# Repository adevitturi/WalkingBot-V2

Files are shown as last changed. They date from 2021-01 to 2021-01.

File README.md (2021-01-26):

# WalkingBot-V2
WalkingBot-V2 is an open source 3D printed robot that walks!
This repository contains all the software, 3D models and BOM to make the full assembly.

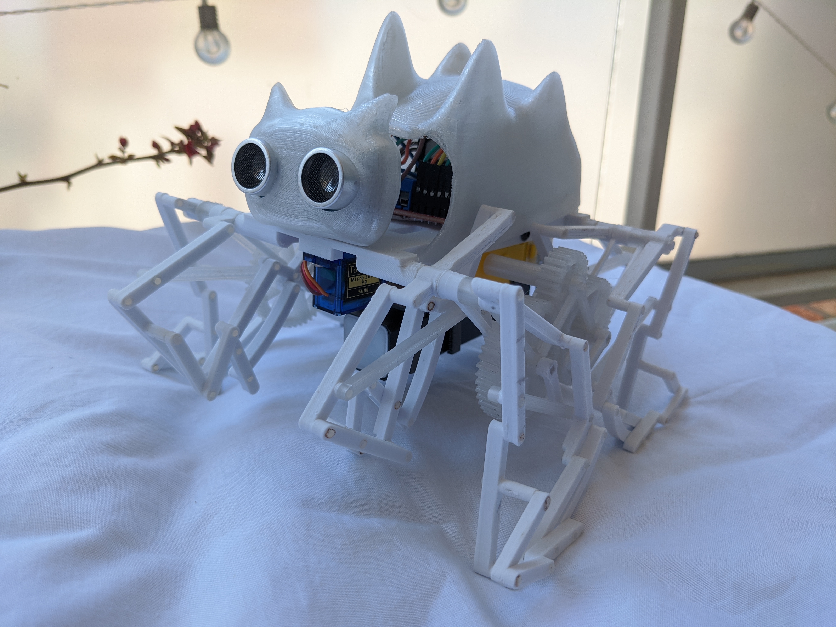
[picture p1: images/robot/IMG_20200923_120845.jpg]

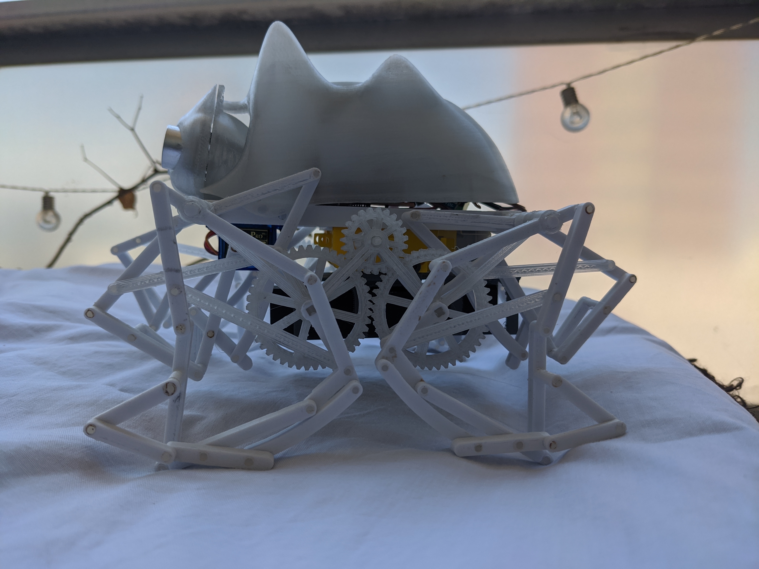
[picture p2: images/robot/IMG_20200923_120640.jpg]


## About
I think my strongest motivation for building walking mechanisms arised after discovering the marvelous [strandbeests by Theo Jansen][1].
After doing some further research on the topic, I found some other mechanimsms with different walking profiles. The one that caught my attention the most was the [trotbot][2], so I based my design on it, adding just some small modifications to the linkage structure.

## Hardware
The following table lists the BOM:

|Parts | Quantity | 
|---|---|
| [NodeMCU board][3] | 1 |
| [L298 N H-Bridge driver][4]  | 1 |
| [18650 battery holder][5] | 1 |
| [18650 batteries][6] | 2 |
| [BMS 2S battery charger][7]  | 1 |
| [cables and connectors][11]  | 2 |
| [ultrasound sensor][8] | 1 |
| [dc motors with gearbox][9]  | 2 |
| [SG90 Servo 180 degrees][10] | 1 	 |
| M3x25 bolts | 4 	 |
| M3x12 bolts | 2 	 |
| M3 nuts | 4 	 |
 
 To see the circuit diagram [click here!](docs/circuit_diagram.md)
 
 ## 3D printed parts and assembly
 STL files can be found under [parts/STL](parts/STL).
 
 The parts were designed using Autodesk Inventor. CAD files and full assemblies can be found under [parts/CAD](parts/CAD).
 
 To see the assembly instructions [click here!](docs/assembly.md)
 
 ## Software
 The robot can be controlled throw Wi-Fi using MQTT messages. For this project we see how to control it with a joystick on an Android App called [Remote XY][12].
 
 The software in this repository includes:
  - Firmware: Arduino sketch for the NodeMCU board.
  - Node-RED flow: a server in charge of communicating the joystick in the phone with the robot.

 To see a guide for setting up the software [click here!](docs/software.md)
 
 ## Videos
 https://youtu.be/vDro2LflieM

 https://youtu.be/8G8XOwB4iCY

 https://youtu.be/JpEi38m9lwI
 
 https://youtu.be/GgEGYwh3bX8
  
 ## Authors

- [Agustin Devitturi](https://github.com/adevitturi)

[1]: https://www.strandbeest.com/
[2]: https://www.diywalkers.com/trotbot-linkage-plans.html
[3]: https://www.amazon.com/KeeYees-Internet-Development-Wireless-Compatible/dp/B07PR9T5R5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 "NodeMcu"
[4]: https://www.amazon.com/L298N-H-Bridge-Stepper-Module-Arduino/dp/B07D2BTMPK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 "L298 Driver"
[5]: https://www.amazon.com/HTTX-Battery-Holder-2-Slot-Storage/dp/B07DBLY3WS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 "Battery holder"
[6]: https://www.ebay.com/itm/SAMSUNG-ICR-22P-SDI-2-GN1T-RECHARGEABLE-BATTERIE-3-6V-2150mAh-Li-Ion-NEU/143293064204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 "18650 batteries"
[7]: https://www.amazon.com/-/es/Li-ion-Bater%C3%ADa-Cargador-Protecci%C3%B3n-Sobrecarga/dp/B07GX2VTXC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 "BMS 2S"
[8]: https://www.amazon.com/UIOTEC-Operating-HC-SR04-P-Ultrasound-Ultrasonic/dp/B07DWWTT3F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 "Ultrasound sensor"
[9]: https://www.amazon.com/AutoEC-4pcs-Motor-Smart-Robot/dp/B00U4HP0SQ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
[10]: https://www.amazon.com/SunFounder-Digital-Helicopter-Airplane-Controls/dp/B01M5LIKLQ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 "Servo"
[11]:https://www.amazon.com/-/es/10-pares-Connector-Battery-discharge-alambre/dp/B01JUDP5NY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 "Battery connector"
[12]:https://play.google.com/store/apps/details?id=com.shevauto.remotexy.free&hl=es&gl=US

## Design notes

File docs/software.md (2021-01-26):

## Arduino firmware
First you need to install Arduino IDE. you can see an installation guide [here][1].

Download the arduino sketch from [firmware/walkingbot](../firmware/walkingbot).
To upload an arduino sketch to the NodeMcu board you can follow [this guide][2].

The firmware on the NodeMcu subscribes to an MQTT topic `diff_speed` to get the linear and angular speed commands in a range from 0 to 100 to command the motors that drive the leags on each side of the robot.
It also subscribes to the topic `head_dir` that commands the movement of the head. Note that the current model of the head doesn't have a really wide angle of movement. This will be tackled in future versions no make for a wider vision angle.
The firmware also publishes constantly the readings from the ultrasound sensor to the topic `ultrasound`, which represents the distance in centimeters.

## Node-RED
You will require to install Node-RED in your pc. You can see an installation guide [here][3].

You will also need to install and run a MQTT broker. You can use Eclipse Mosquitto, which is an open-source MQTT message broker. You can see an installation guide [here][4].

Once you have node-RED running, download the Node-RED flow from [nodered/robot-control.json](../nodered/robot-control.json) and import it in your browser.
Then you can make sure that all nodes are set up properly and finally click the 'Deploy' button.

## Android Remote XY
You can download the [Remote XY][5] app to your Android device.
Once you run it, you can go to the '+' option, then 'connect to device by IP or URL'.
In the 'Device IP or URL' field enter your local IP address, on which node-RED is running.
In the 'Port' field you can check the selected port in the node-RED configuration for the nodes using Remote XY, in general it is 6377.
Finally you should see a dashboard with a joystick and a control to move the head and see the distance reading.

You can edit the current dashboard in the [Remote XY Editor][6] and then paste the generated code in any node configuration for Remote XY in your node-RED flow.

[1]: https://www.arduino.cc/en/software
[2]: https://www.instructables.com/Quick-Start-to-Nodemcu-ESP8266-on-Arduino-IDE/
[3]: https://nodered.org/docs/getting-started/local
[4]: https://mosquitto.org/download/
[5]: https://play.google.com/store/apps/details?id=com.shevauto.remotexy.free&hl=es&gl=US
[6]: https://remotexy.com/en/editor/

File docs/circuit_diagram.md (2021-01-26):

## Circuit diagram

You can see the whole diagram in the picture below. Or access the image under [images/circuit/circuit_diagram.png](../images/circuit/circuit_diagram.png).

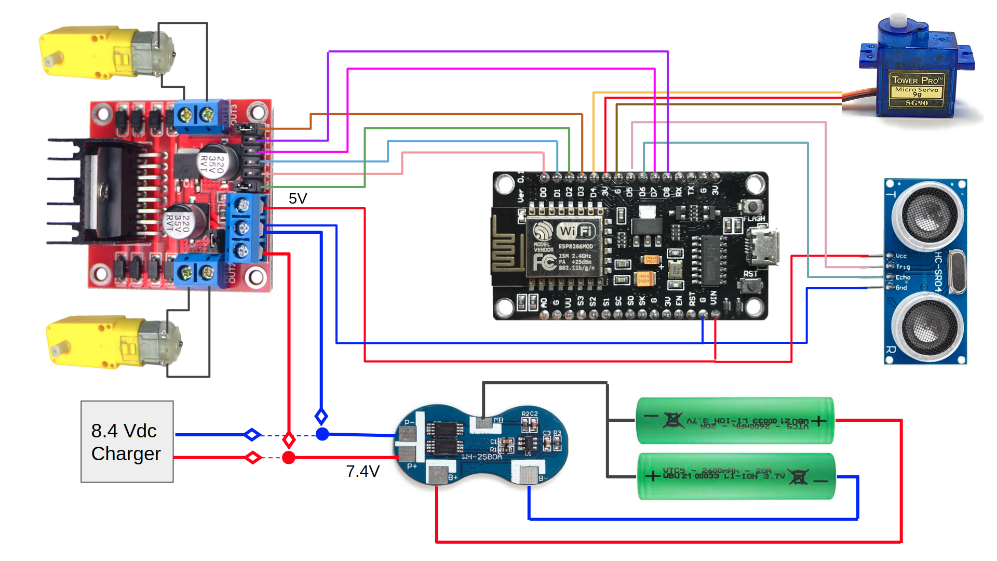
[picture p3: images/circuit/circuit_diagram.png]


To connect all the wires that come out from the NodeMcu you can assemble a small development board with some extra male header pins to make it easier, but you can choose the way that is easier to you.
In the following picture you can see an example board with some extra header pins to connect some dupont cables.

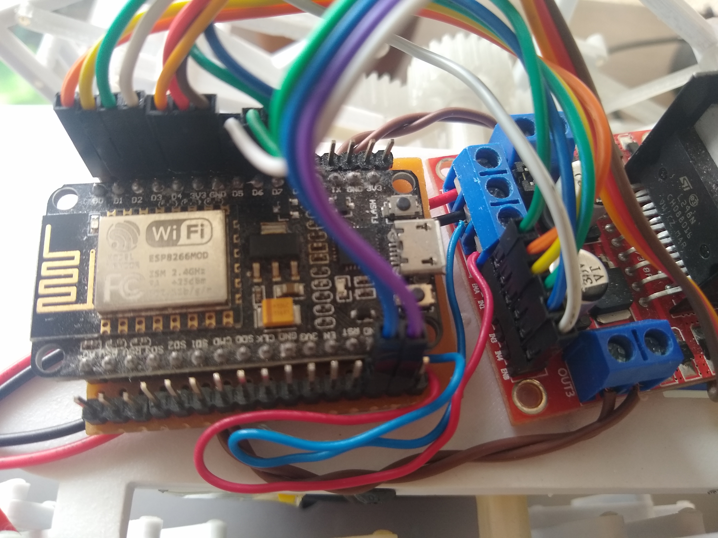
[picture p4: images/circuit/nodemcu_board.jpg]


You will notice that to make the connections in the robot head there is a hole where you can connect some duppont cables.

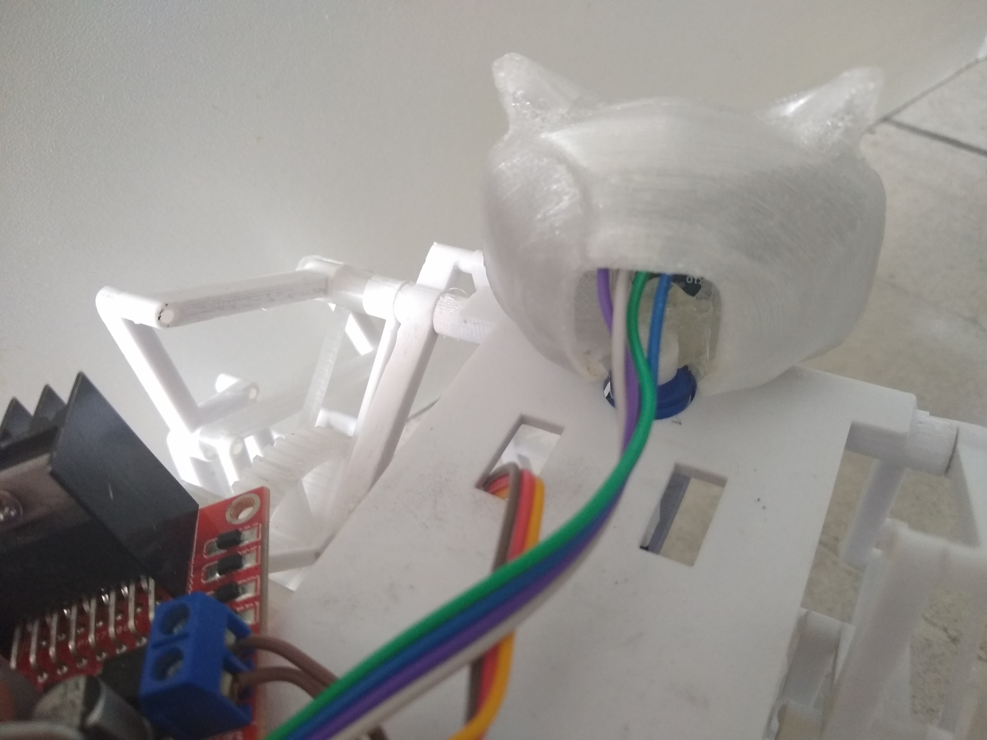
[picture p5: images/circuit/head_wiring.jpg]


To connect the motors, the servo and the batteries, you will notice there are some square holes in the robot chasis from where you can pull the cables from the other side.

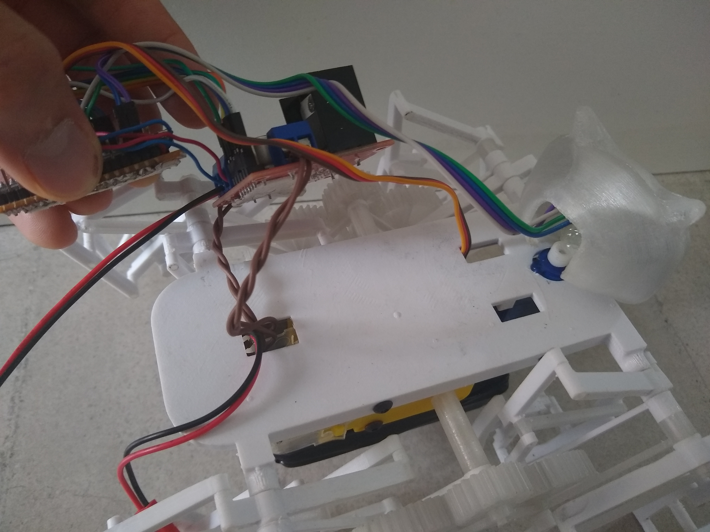
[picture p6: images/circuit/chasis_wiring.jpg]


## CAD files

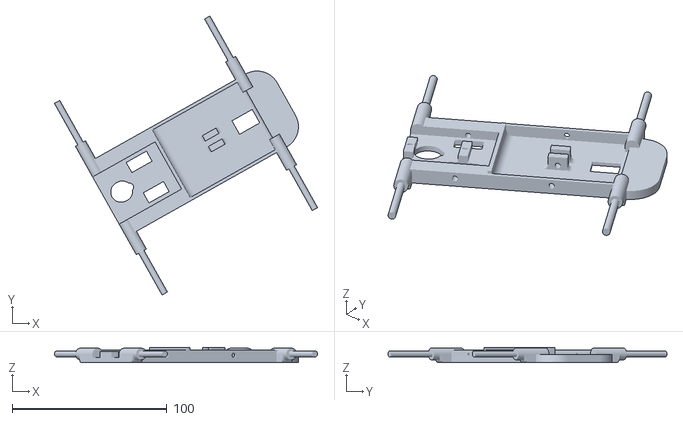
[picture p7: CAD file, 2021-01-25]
parts/STL/body/chasis.stl
170.1 x 180.3 x 9.42

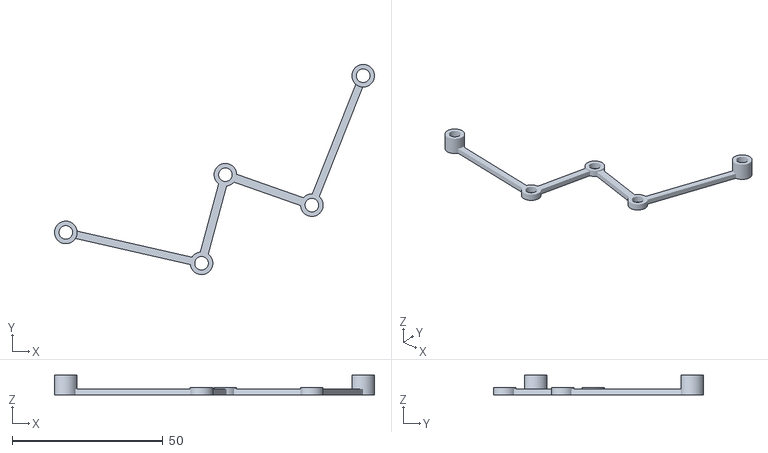
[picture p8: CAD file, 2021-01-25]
parts/STL/gears/gear-holder.stl
106.0 x 69.6 x 6.50

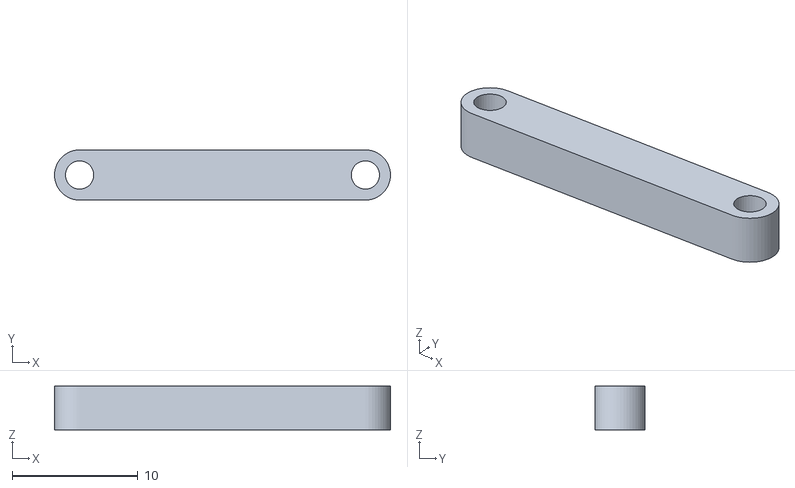
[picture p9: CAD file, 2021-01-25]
parts/STL/leg/toe1.stl
26.8 x 4.00 x 3.50

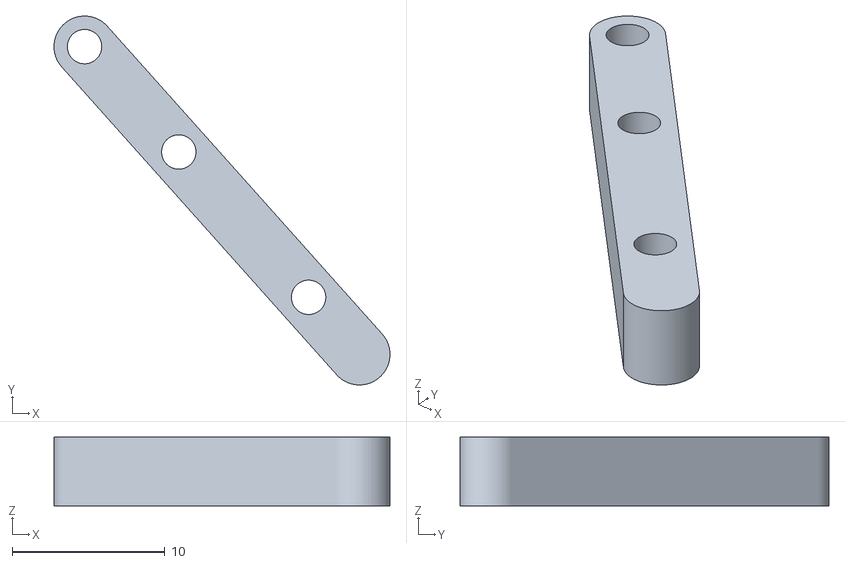
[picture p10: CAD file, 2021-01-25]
parts/STL/leg_mirrored/bone3_MIR.stl
22.0 x 24.1 x 4.50

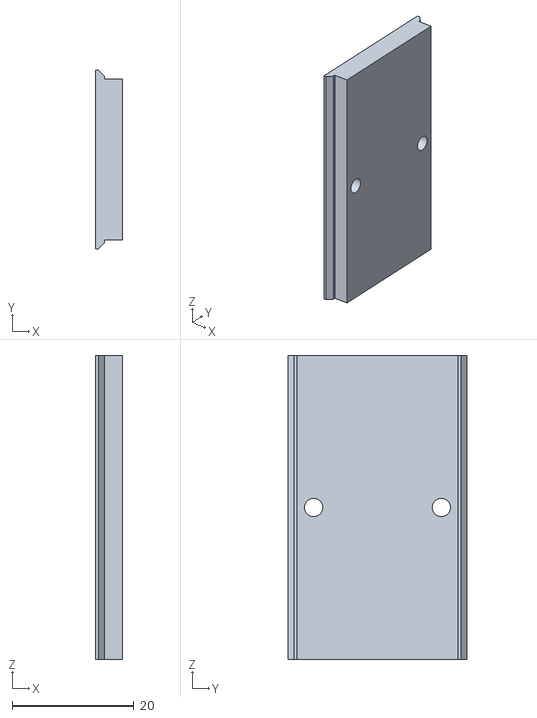
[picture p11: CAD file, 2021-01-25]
parts/STL/body/batter-holder.stl
4.50 x 29.5 x 50.0

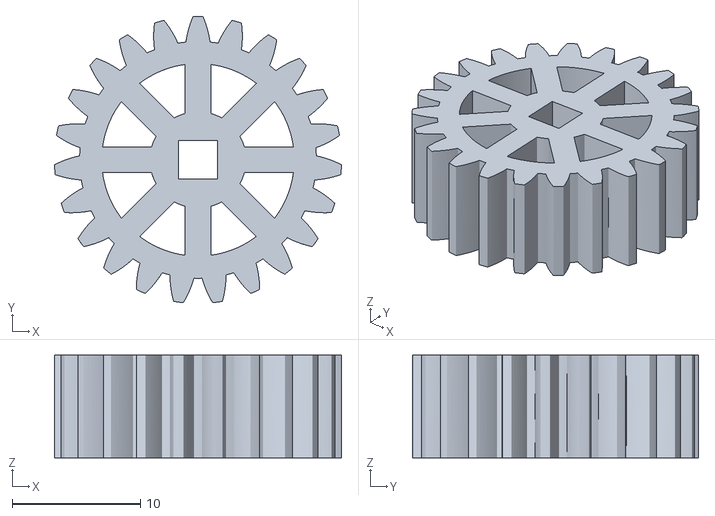
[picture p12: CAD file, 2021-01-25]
parts/STL/gears/small-gear.stl
22.4 x 22.3 x 8.00

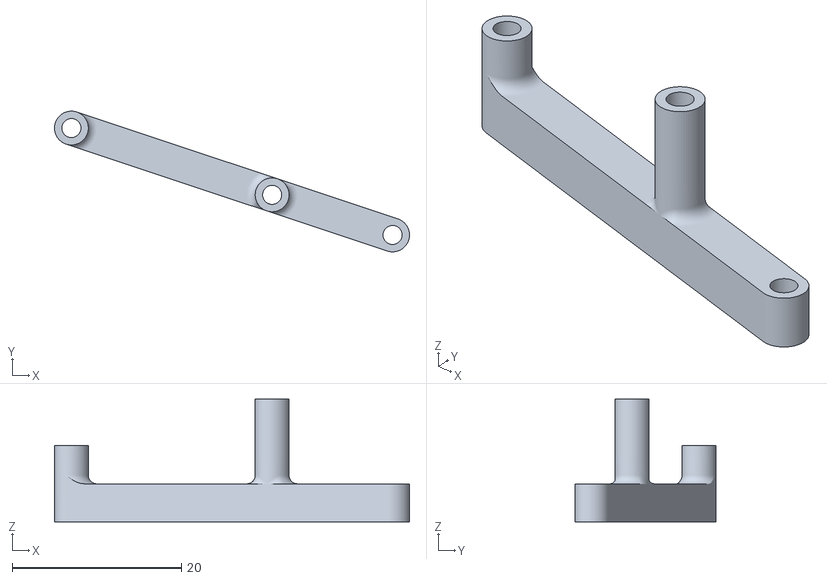
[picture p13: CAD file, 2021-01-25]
parts/STL/leg/bone4.stl
42.0 x 16.6 x 14.5

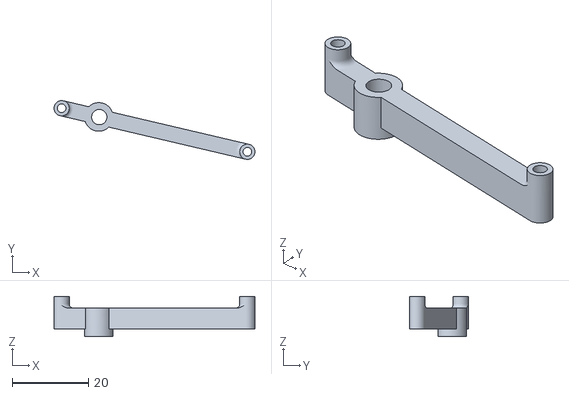
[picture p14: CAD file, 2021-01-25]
parts/STL/leg_mirrored/bone0_MIR.stl
52.7 x 15.4 x 10.5

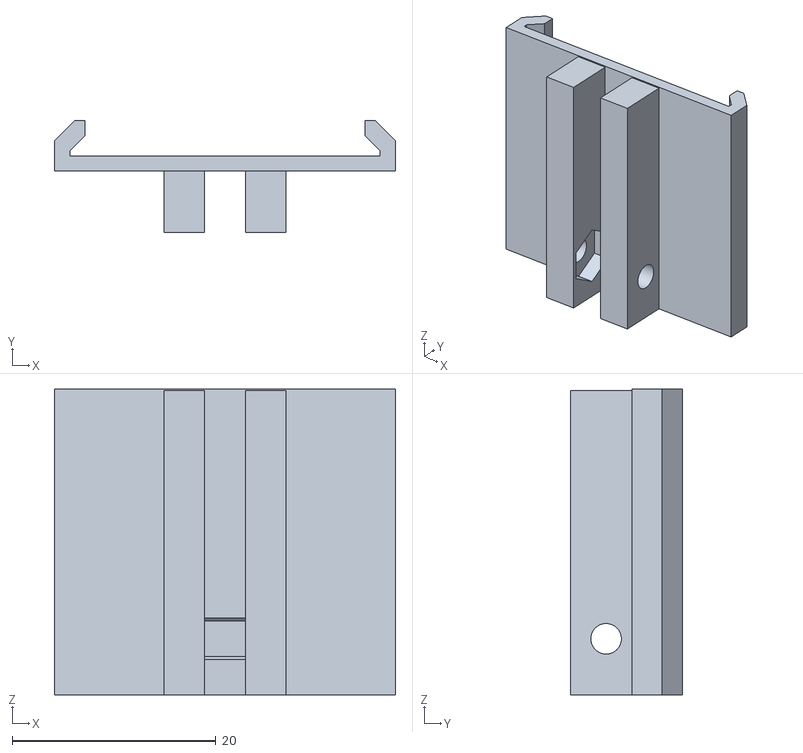
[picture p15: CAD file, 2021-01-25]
parts/STL/body/battery-holder-robot.stl
33.5 x 11.0 x 30.0

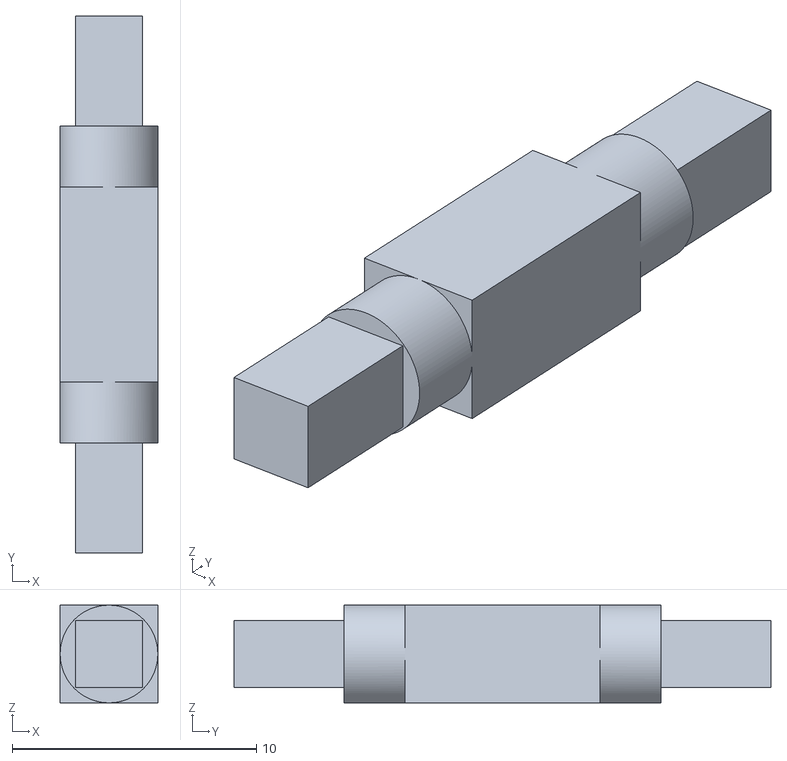
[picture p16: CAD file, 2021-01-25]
parts/STL/gears/gear2-shaft.stl
4.00 x 22.0 x 4.00

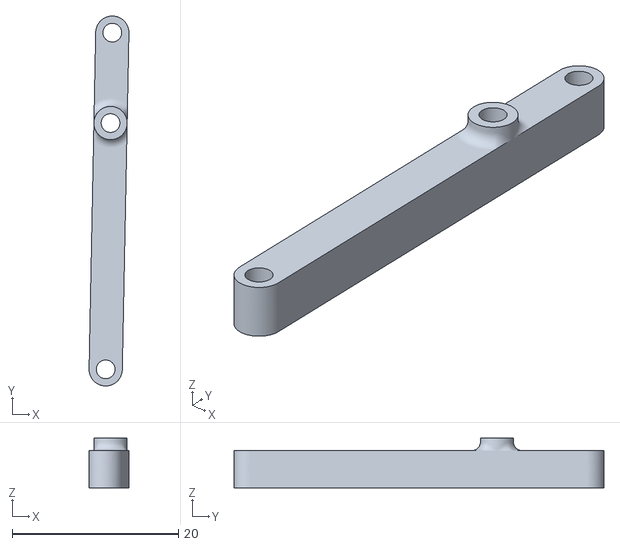
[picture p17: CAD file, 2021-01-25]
parts/STL/leg/bone5.stl
4.80 x 44.5 x 6.00

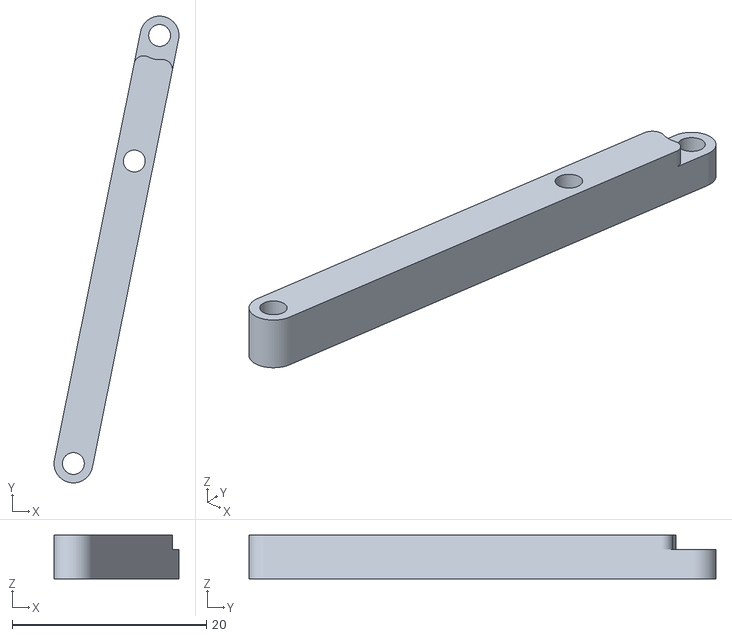
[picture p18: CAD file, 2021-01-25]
parts/STL/leg_mirrored/bone1_MIR.stl
12.9 x 48.1 x 4.50

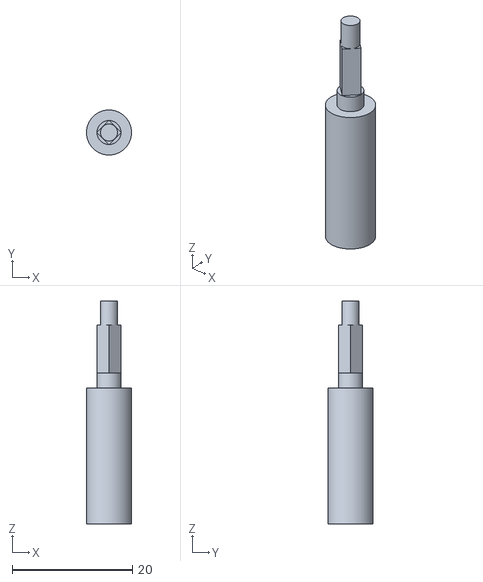
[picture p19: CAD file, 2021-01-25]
parts/STL/gears/gear1-shaft.stl
7.50 x 7.50 x 37.1

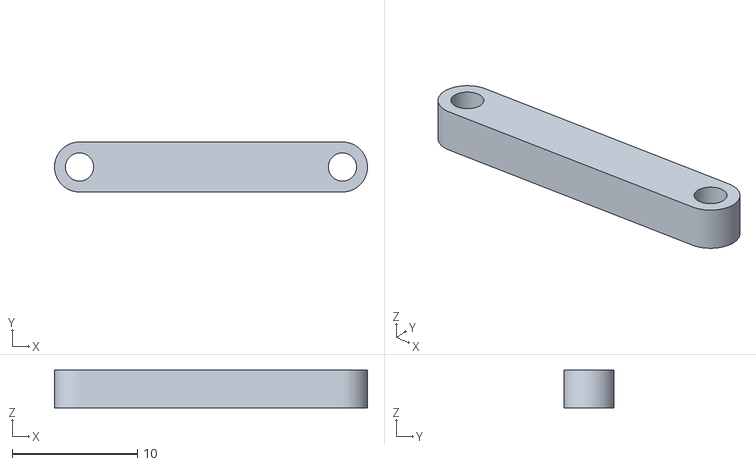
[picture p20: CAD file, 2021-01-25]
parts/STL/leg/toe2.stl
25.0 x 4.00 x 3.00

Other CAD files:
parts/STL/leg_mirrored/bone6_MIR.stl
parts/STL/gears/big-gear.stl
parts/STL/leg/bone2.stl
parts/STL/leg_mirrored/bone5_MIR.stl
parts/CAD/DCMotor.ipt
parts/CAD/Servo.ipt
parts/CAD/base-bone.ipt
parts/CAD/base-bone_MIR.ipt
parts/CAD/batter-holder.ipt
parts/CAD/battery-holder-robot.ipt
parts/CAD/big-gear.ipt
parts/CAD/bone0.ipt
parts/CAD/bone0_MIR.ipt
parts/CAD/bone1.ipt
parts/CAD/bone1_MIR.ipt
parts/CAD/bone2.ipt
parts/CAD/bone2_MIR.ipt
parts/CAD/bone3.ipt
parts/CAD/bone3_MIR.ipt
parts/CAD/bone4.ipt
parts/CAD/bone4_MIR.ipt
parts/CAD/bone5.ipt
parts/CAD/bone5_MIR.ipt
parts/CAD/bone6.ipt
parts/CAD/bone6_MIR.ipt
parts/CAD/bone7.ipt
parts/CAD/bone7_MIR.ipt
parts/CAD/chasis.ipt
parts/CAD/dc-driver.ipt
parts/CAD/gear-holder.ipt
parts/CAD/gear1-shaft.ipt
parts/CAD/gear2-shaft.ipt
parts/CAD/head.ipt
parts/CAD/leg_assembly.iam
parts/CAD/node-mcu.ipt
parts/CAD/robot-side-assembly.iam
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

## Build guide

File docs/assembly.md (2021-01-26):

## Leg assembly

The robot uses 8 legs distributed in pairs. Each pair consists of a leg and its mirrored version. So in total, the robot requires a set of 4 legs and 4 mirrored legs.

The following table describes the parts required to assembe a single leg. These parts can be found under [parts/STL/leg](../parts/STL/leg).

|Parts | Quantity | 
|---|---|
| base-bone | 1 |
| bone0 | 1 |
| bone1 | 1 |
| bone2 | 1 |
| bone3 | 1 |
| bone4 | 1 |
| bone5 | 1 |
| bone6 | 1 |
| bone7 | 1 	 |
| toe1 | 1 	 |
| toe2 | 1 	 |

To assemle a single mirrored leg, the files are the same, but have the suffix `_MIR`. These parts can be found under [parts/STL/leg_mirrored](../parts/STL/leg_mirrored).

To assemble the different sections of each leg, you can insert a piece of filament through the holes and then use a soldering iron (or a lighter) to melt the sides of the filament. You can see an example [here][1].

First, join base-bone with bone6 and bone7.

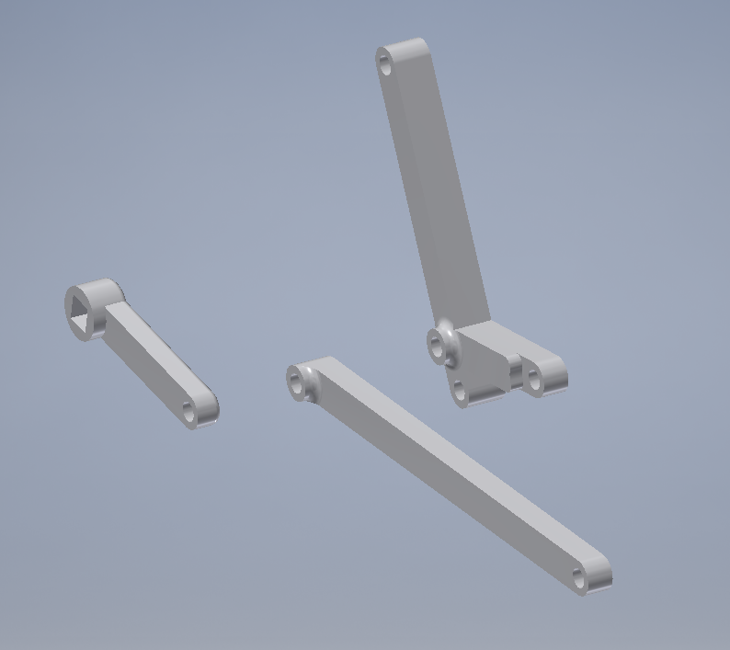
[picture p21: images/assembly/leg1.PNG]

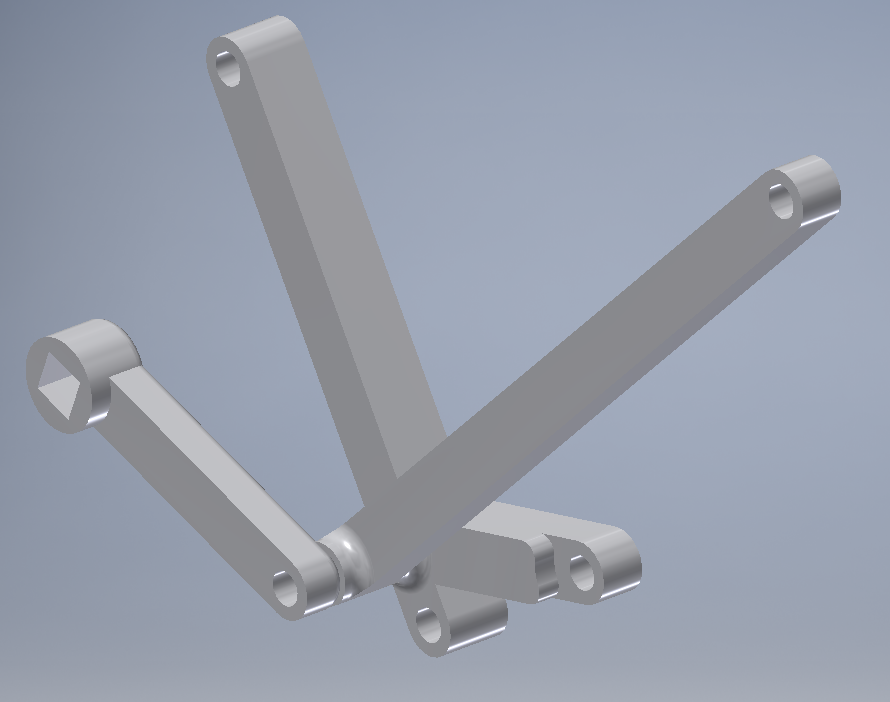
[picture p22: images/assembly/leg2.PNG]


Then add bone1 and bone 2 to the other side of base-bone.

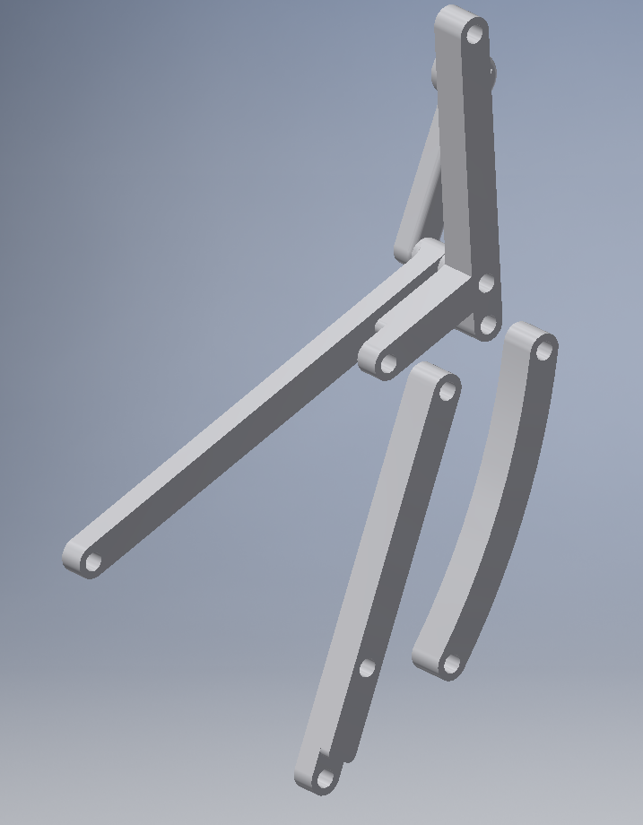
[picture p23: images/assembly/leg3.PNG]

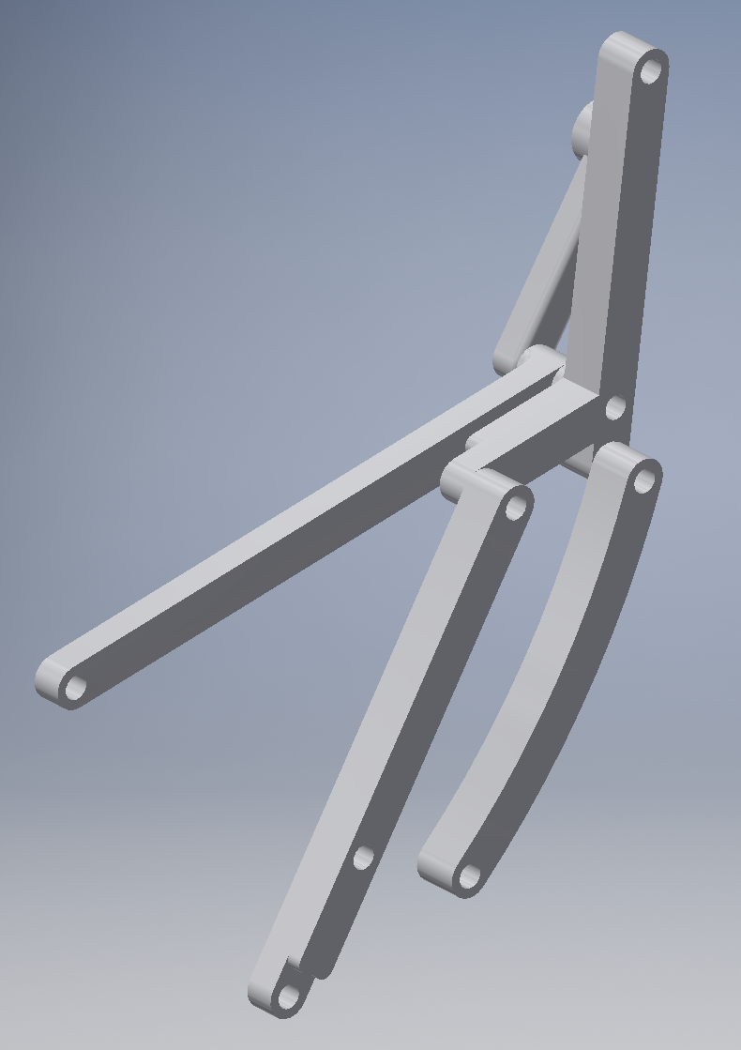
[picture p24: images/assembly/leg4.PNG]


Then join bone4 with bone1 and proceed to attach bone3 to bone1 and bone2.

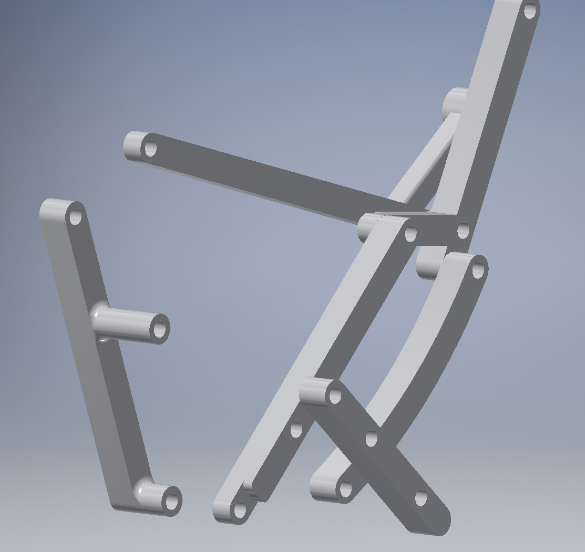
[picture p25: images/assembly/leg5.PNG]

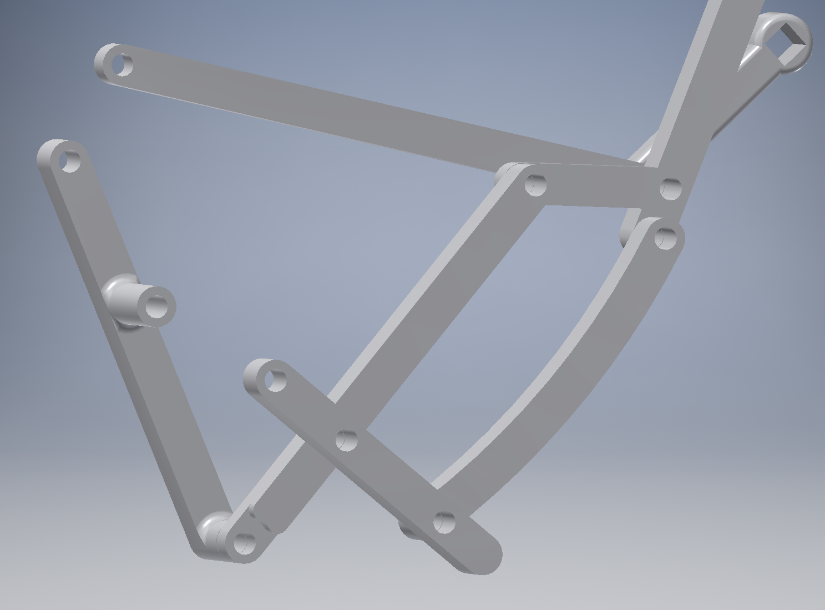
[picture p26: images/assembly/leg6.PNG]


Next join bone4 and bone7 with bone5.

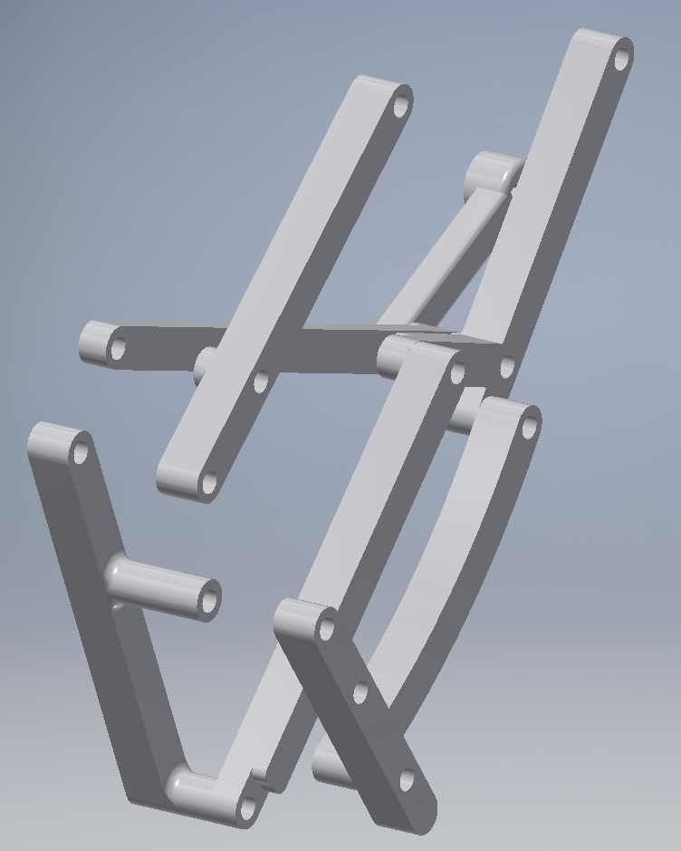
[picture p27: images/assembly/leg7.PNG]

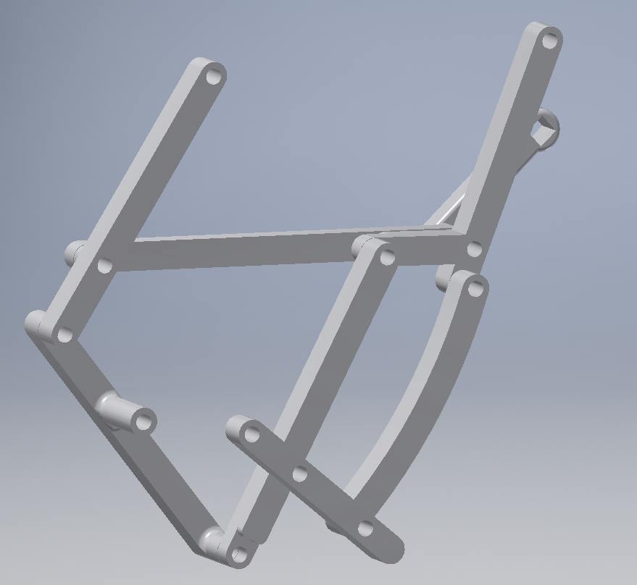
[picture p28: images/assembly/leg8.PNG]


Now join bone5 and base-bone with bone0.

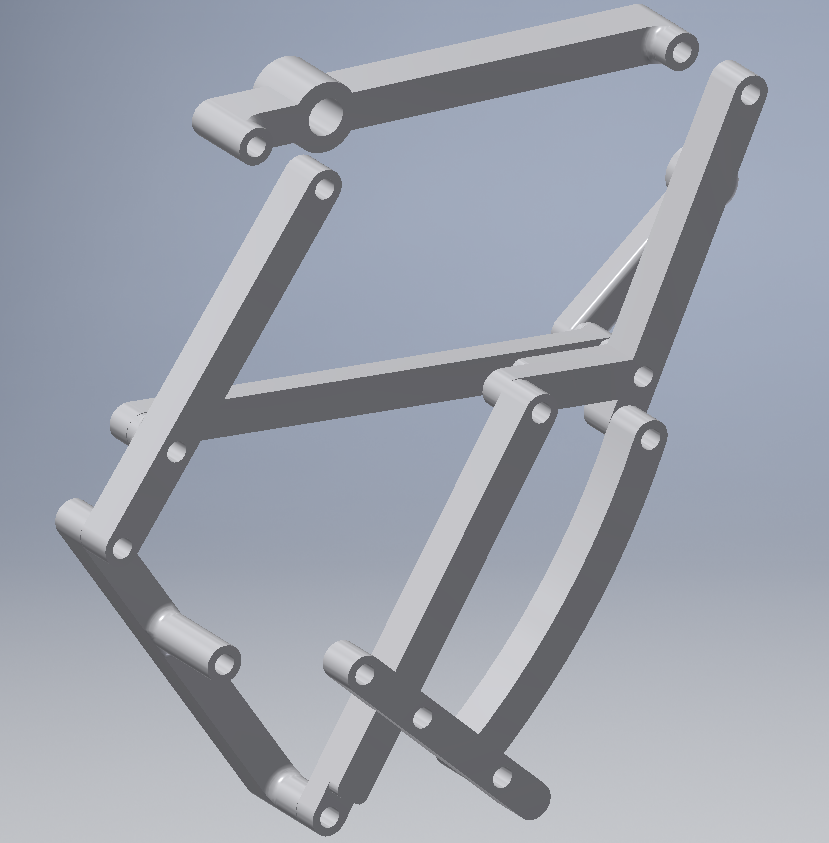
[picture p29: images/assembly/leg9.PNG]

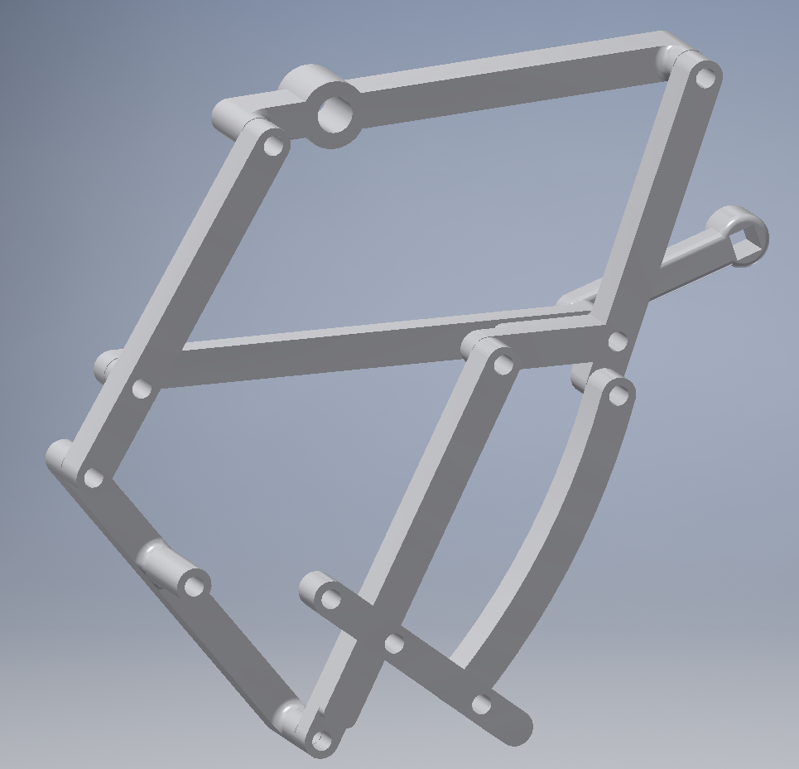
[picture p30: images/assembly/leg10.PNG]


Finally, attach toe1 (the longer one) to bone4 and toe2 (the short one) to bone3.

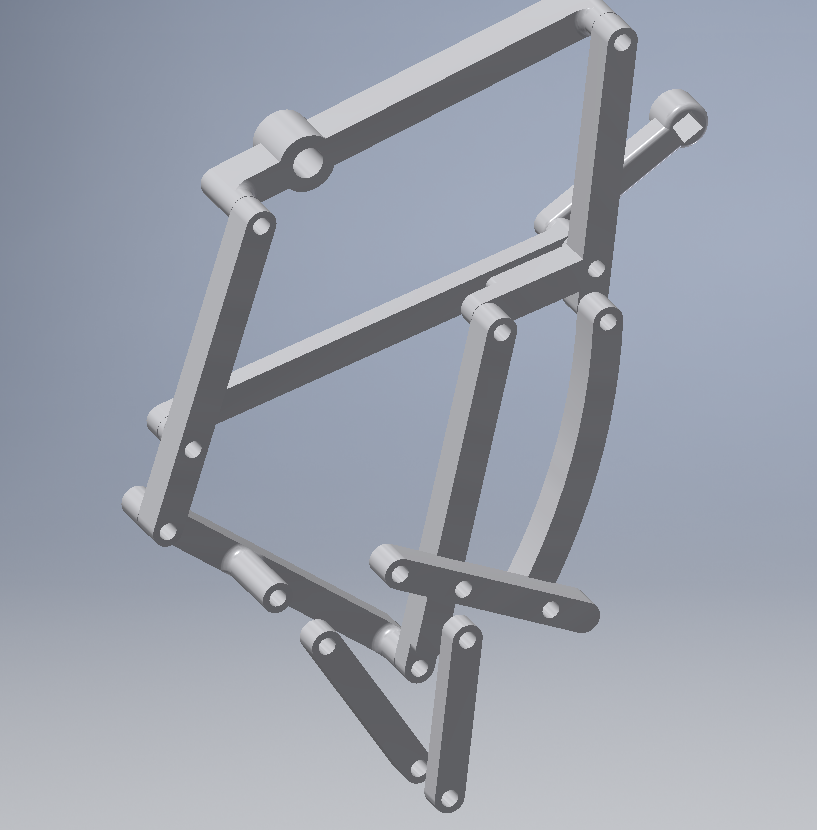
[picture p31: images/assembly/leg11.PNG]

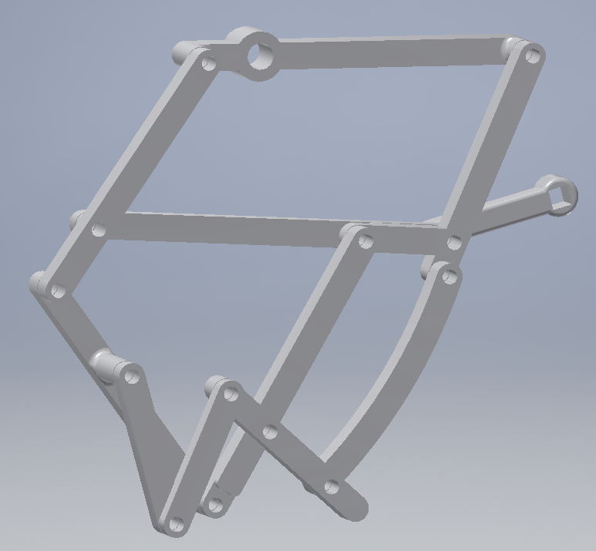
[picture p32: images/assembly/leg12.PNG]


## Body Assembly
For the body you need to print 3 parts, located under [parts/STL/body](parts/STL/body). You will also need 2 DC motors, 1 Servo and some bolts and nuts.
|Parts | Quantity | 
|---|---|
| chasis | 1 |
| battery-holder | 1 |
| battery-holder-robot | 1 |
| M3x25 bolts | 4 |
| M3 nuts | 4 |
| DC motors | 2 |
| Sg90 Servo | 1 |

First place the DC motors inside the chasis. You will notice that in the inside between them you can place 2 M3 nuts (can be optional if the bolts fit correctly on your print).
Then proceed to screw the M3x25 bolts to fasten the motors to the chasis.
Now you can put the battery-holder-robot part in the middle of the motors. Note that this part also has space for 2 M3 nuts. Proceed to fasten this part to the motors with the other 2 M3x25 bolts.
Then you can place the Servo with its shaft going through the chasis and fasten it with its set of screws (normally sold as misc with the servo).

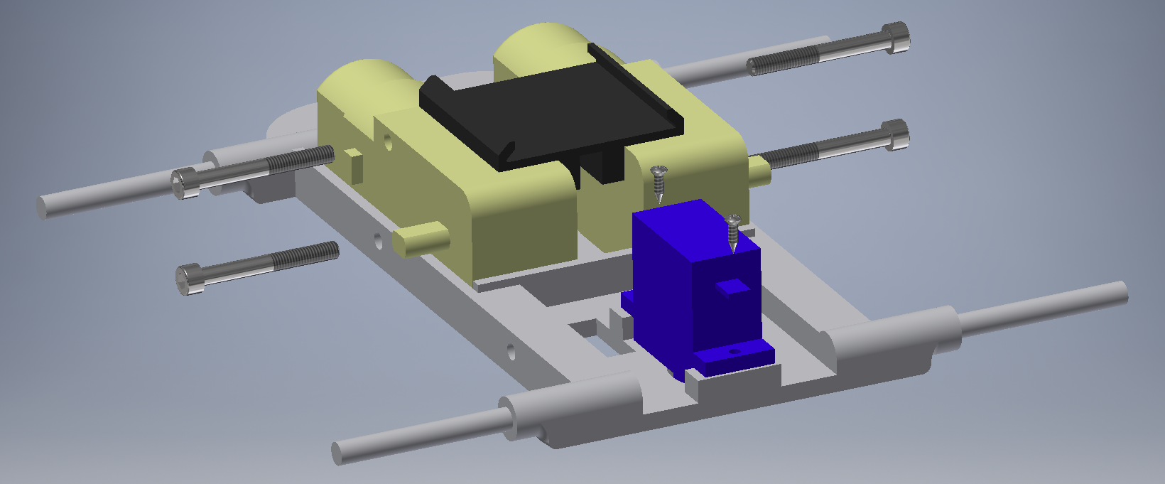
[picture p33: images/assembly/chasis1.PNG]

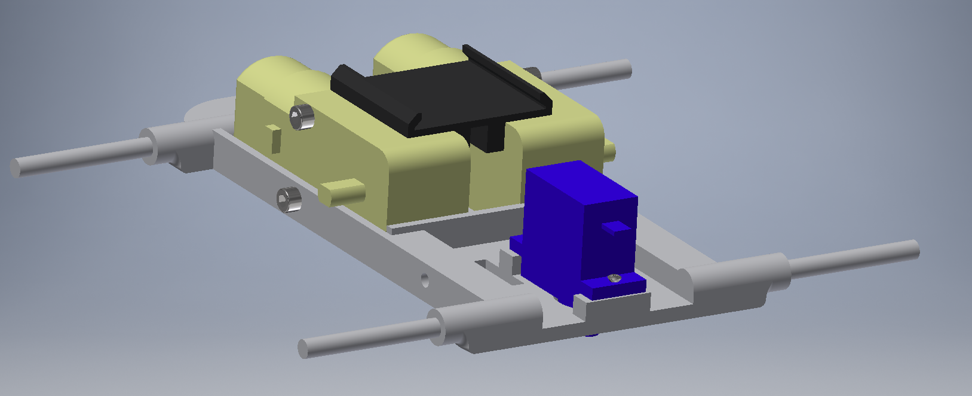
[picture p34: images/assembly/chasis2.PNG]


Finally you can attach the battery-holder 3D printed part to your real 18650 battery holder (you can glue it or drill two M3 holes to the holder to fasten it to the printed part with 2 extra M3 bolts). Note that the battery-holder part slides inside the battery-holder-robot part. That way the robot can lift the batteries and at the same time they are easy to remove.

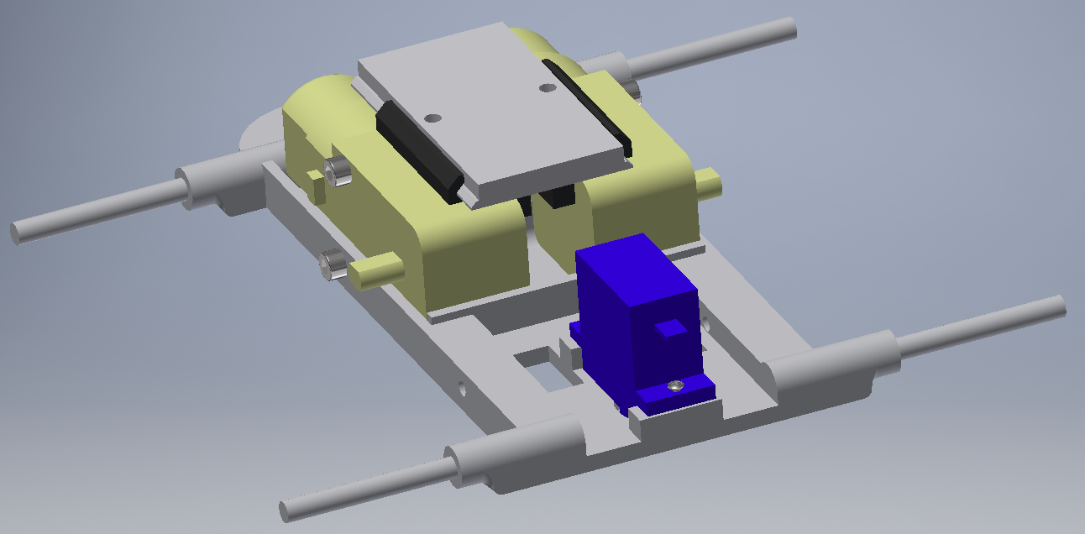
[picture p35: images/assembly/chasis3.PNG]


## Full assembly
For the rest of the assembly you will need parts that can be found under [parts/STL/body](../parts/STL/body) and [parts/STL/gears](../parts/STL/gears).
You will need:

|Parts | Quantity | 
|---|---|
| assembled legs | 4 |
| assembled mirrored legs | 4 |
| body assembled in previous step | 1 |
| big-gear | 4 |
| small-gear | 2 |
| gear-holder | 4 |
| gear1-shaft | 2 |
| gear2-shaft | 4 |
| head-bottom | 1 |
| heat-top | 1 |
| shell | 1 |
| printed washers | 4 |

First place two legs in the chasis cilinders and insert a gear1-shaft adapter in the dc motor shaft as shown in the picture below.
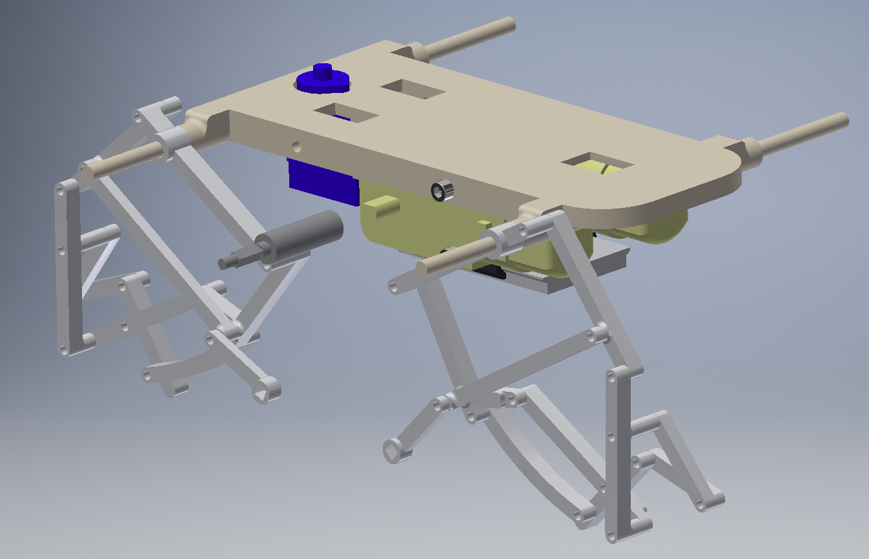
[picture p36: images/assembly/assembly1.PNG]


Then place a gear-holder part that should fit in the chasis cilinders and in the gear1-shaft adapter. Insert 1 small-gear into the gear1-shaft. Now insert a gear2-shaft in each of the 2 big gears, and then place them in the remaining holes of the gear-holder. Note that the sides of the gear2-shaft parts should fit inside the bone6 square holes, coupling the gears to the legs. Finally place another gear-holder part to hold the gears in place.
One important thing to take into account is that the bone6 parts of each legs should be shifted by a 90 degree angle between them, so that both legs don't collide with each other as they move.

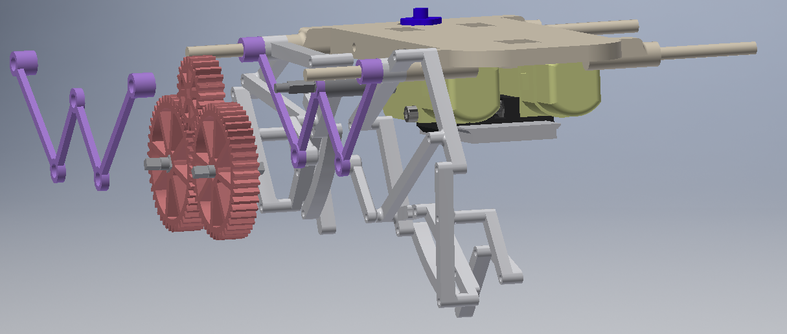
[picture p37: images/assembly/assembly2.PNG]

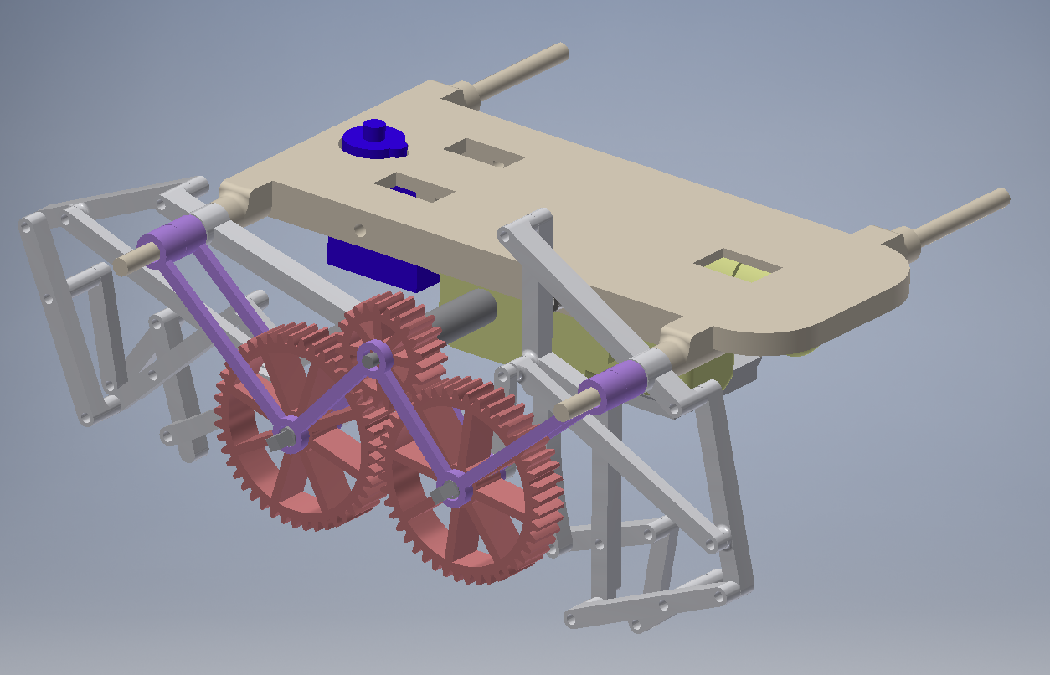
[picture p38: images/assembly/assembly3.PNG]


Now you can place the other pair of legs that should fit in the chasis cilinder and by coupling the bone6 parts with the gear2-shafts. Finally insert two washer parts to hold the legs in place.

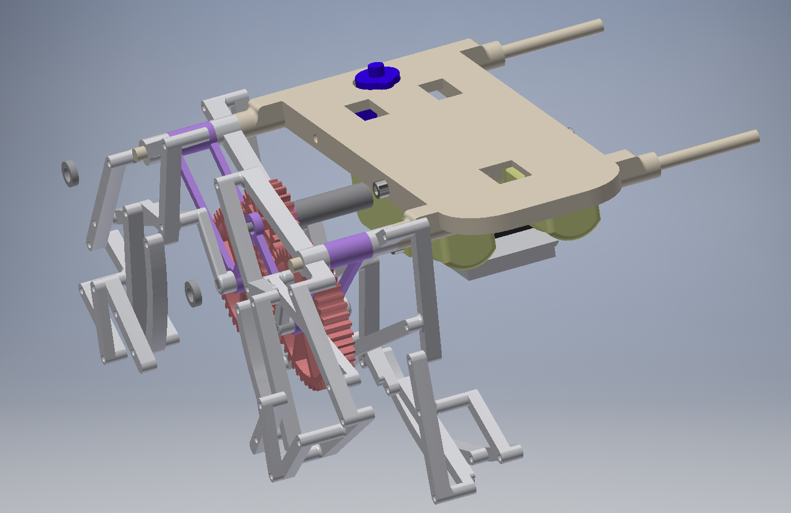
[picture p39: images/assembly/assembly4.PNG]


In the pictures below you can see how the legs in different chasis cilinders showld be shifted 90 degrees, while legs in the same chasis cilinder should be shifted 180 degrees.

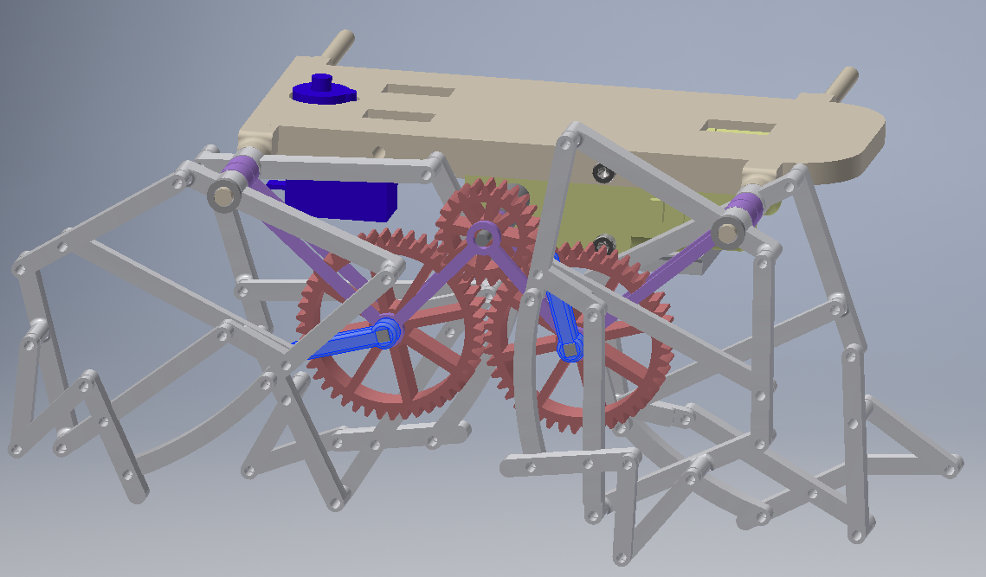
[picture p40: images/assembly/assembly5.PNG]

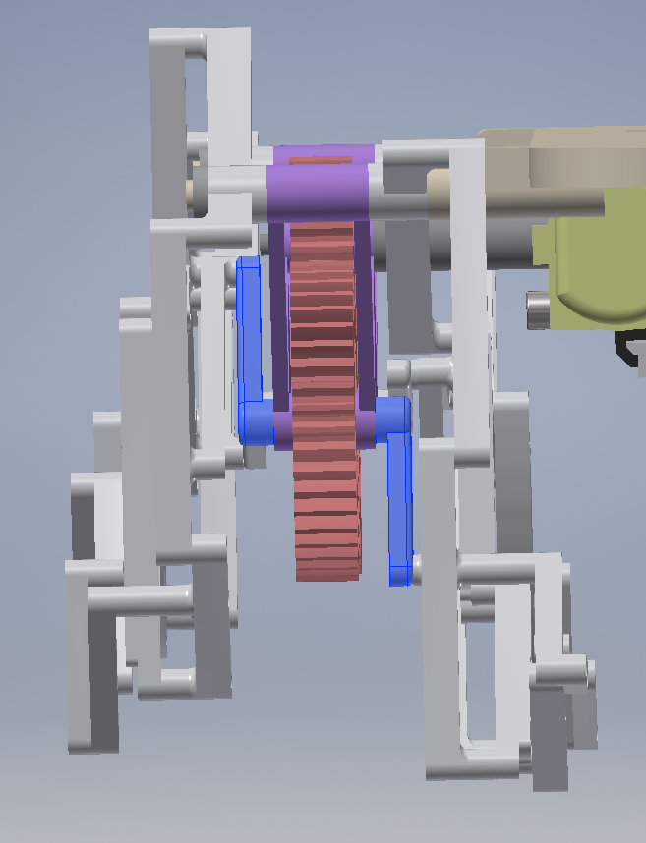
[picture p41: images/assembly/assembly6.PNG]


Now you can follow this same steps to assemble the other side of the robot with its gears and the remaining 4 legs.

The next step is to print the 2 parts of the head, place the ultrasound sensor inside and glue the parts together.

Once that is complete, you can place the hardware in top of the robot (NodeMcu and H bride motor drive) and finish wiring the boards, dc motors, the servo and ultasound sensor. You can hold the robot head in the Servo shaft (that normally comes as a misc part). To fix the head to the servo shaft you can glue it e.g. by using a glue gun. Finally you can place the shell on top of the electronics, and you can fasten it to the chasis with 2 M3x12 bolts.

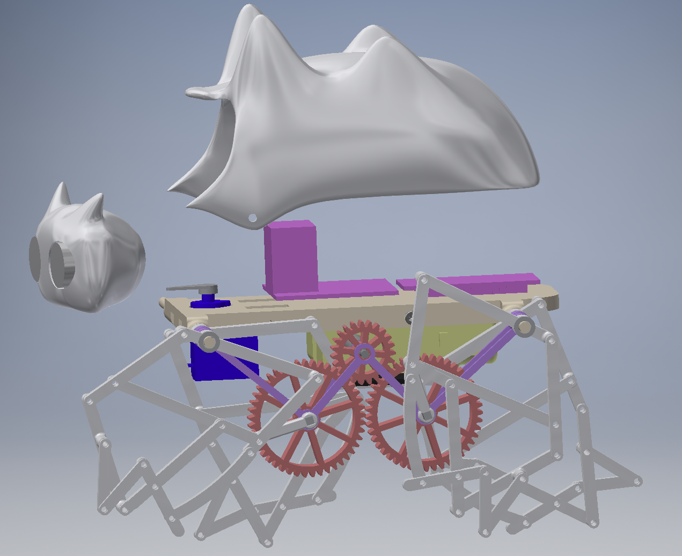
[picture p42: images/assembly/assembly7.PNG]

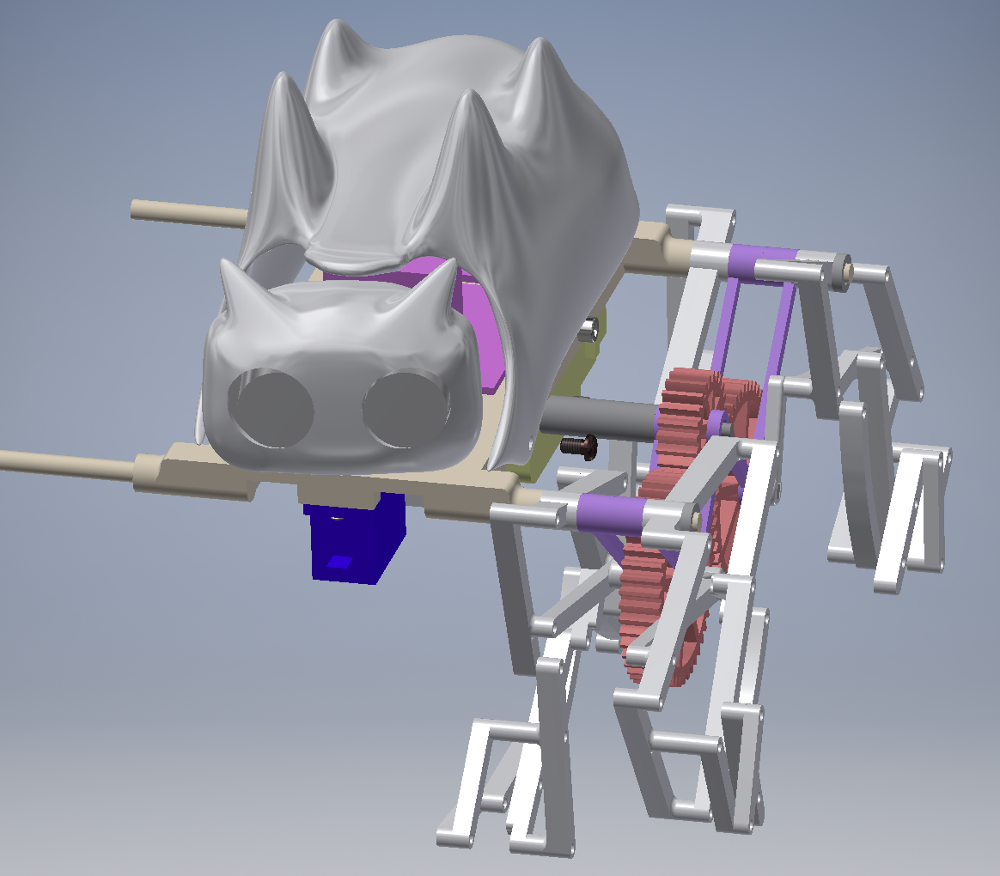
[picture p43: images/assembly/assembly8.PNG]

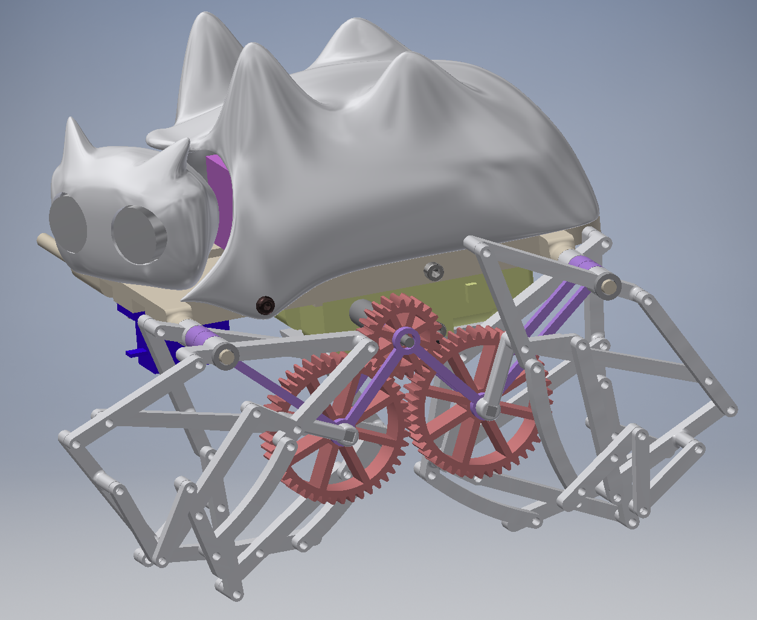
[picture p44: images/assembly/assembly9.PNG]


[1]: https://www.youtube.com/watch?v=RxB7USuMwRw&feature=youtu.be

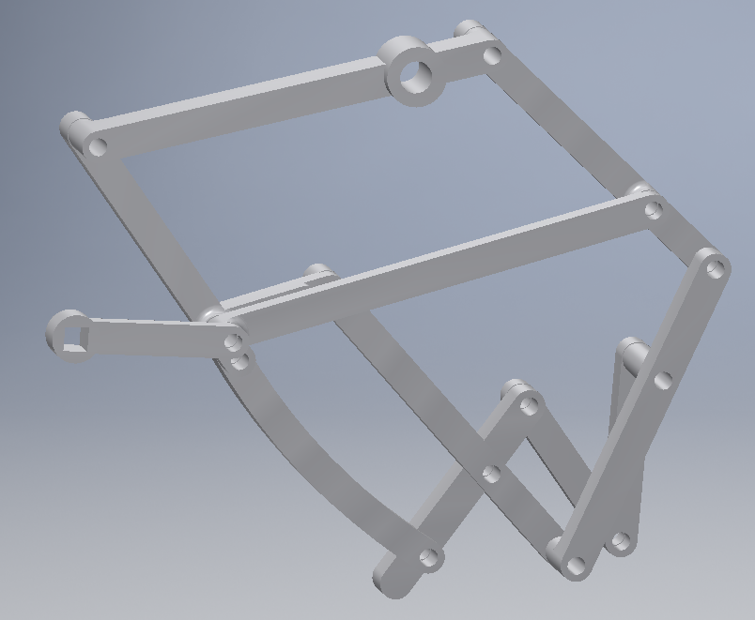
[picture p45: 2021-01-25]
images/assembly/leg13.PNG

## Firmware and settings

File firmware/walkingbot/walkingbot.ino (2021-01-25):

/*
Copyright (c) 2017, Agustin Devitturi (agustin.devitturi@gmail.com)
  This library is free software; you can redistribute it and/or
  modify it under the terms of the GNU Lesser General Public
  License as published by the Free Software Foundation; either
  version 2.1 of the License, or (at your option) any later version.
  This library is distributed in the hope that it will be useful,
  but WITHOUT ANY WARRANTY; without even the implied warranty of
  MERCHANTABILITY or FITNESS FOR A PARTICULAR PURPOSE.  See the GNU
  Lesser General Public License for more details.
  You should have received a copy of the GNU Lesser General Public
  License along with this library; if not, write to the Free Software
  Foundation, Inc., 51 Franklin St, Fifth Floor, Boston, MA  02110-1301  USA
*/

// https://www.arduino.cc/reference/en/libraries/pubsubclient/
// https://arduinojson.org/v6/assistant/ to compute the static json size.

#include "dcmotor.h"
#include "servo.h"
#include <ESP8266WiFi.h>
#include <PubSubClient.h>
#include <ArduinoJson.h>
#include <HCSR04.h>

#define MOTOR_EN_A  4
#define MOTOR_EN_B  0
#define MOTOR_DIR_IN1  16
#define MOTOR_DIR_IN2  5
#define MOTOR_DIR_IN3  13
#define MOTOR_DIR_IN4  15
#define SERVO_HEAD 2
#define ULTRASOUND_TRIG 14
#define ULTRASOUND_ECHO 12

#define MSG_BUFFER_SIZE  (50)

L298N::DcMotors dcmotors(MOTOR_EN_A, MOTOR_EN_B, MOTOR_DIR_IN1, MOTOR_DIR_IN2, MOTOR_DIR_IN3, MOTOR_DIR_IN4);
TowerPro::Servo servo_head(SERVO_HEAD, 50);
HCSR04 hc(ULTRASOUND_TRIG, ULTRASOUND_ECHO);//initialisation class HCSR04 (trig pin , echo pin)

StaticJsonDocument<200> json;

const char* ssid = "YourSSID";
const char* password = "YourSSIDPassword";
const char* mqtt_server = "YourIpAddr";

WiFiClient espClient;
PubSubClient client(espClient);
unsigned long lastMsg = 0;

char msg[MSG_BUFFER_SIZE];
int value = 0;

void setup_wifi() {

  delay(10);
  // We start by connecting to a WiFi network
  Serial.println();
  Serial.print("Connecting to ");
  Serial.println(ssid);

  WiFi.mode(WIFI_STA);
  WiFi.begin(ssid, password);

  while (WiFi.status() != WL_CONNECTED) {
    delay(500);
    Serial.print(".");
  }

  randomSeed(micros());

  Serial.println("");
  Serial.println("WiFi connected");
  Serial.println("IP address: ");
  Serial.println(WiFi.localIP());
}

char payload_buffer[64];
void callback(char* topic, byte* payload, unsigned int length) {
  String topic_str(topic);

  // Form a C-string from the payload
  memcpy(payload_buffer, payload, length);
  payload_buffer[length] = '\0';
  
  String payload_str(payload_buffer);
  payload[length] = '\0';
  Serial.print("Message arrived [");
  Serial.print(topic);
  Serial.print("] ");
  Serial.print(payload_str);
  Serial.println();  

  if (topic_str.equals("diff_speed")) {
    // Deserialize the JSON document
    DeserializationError error = deserializeJson(json, (char *)payload);
  
    // Test if parsing succeeds.
    if (error) {
      Serial.print(F("deserializeJson() failed: "));
      Serial.println(error.f_str());
      return;
    }
  
    int linear = json["linear"];
    int angular = json["angular"];
    dcmotors.set_diff_drive_speed(linear, angular);
    Serial.print("linear: ");
    Serial.println(linear);
    Serial.print("angular: ");
    Serial.println(angular);
  }

  if (topic_str.equals("head_dir")) {
    int value = payload_str.toInt();
    servo_head.go_to_pos(value);
  }  
}

void reconnect() {
  // Loop until we're reconnected
  while (!client.connected()) {
    Serial.print("Attempting MQTT connection...");
    // Create a random client ID
    String clientId = "ESP8266Client-";
    clientId += String(random(0xffff), HEX);
    // Attempt to connect
    if (client.connect(clientId.c_str())) {
      Serial.println("connected");
      // Once connected, publish an announcement...
      client.publish("connection", "connected");
      // ... and resubscribe
      client.subscribe("diff_speed");
      client.subscribe("head_dir");
    } else {
      Serial.print("failed, rc=");
      Serial.print(client.state());
      Serial.println(" try again in 5 seconds");
      // Wait 5 seconds before retrying
      delay(5000);
    }
  }
}

void setup() {
  pinMode(SERVO_HEAD, OUTPUT);
  Serial.begin(115200);
  setup_wifi();
  client.setServer(mqtt_server, 1883);
  client.setCallback(callback); 
}

unsigned long last_loop_time = 0;
unsigned long current_time = 0;
char ultrasound_buff[10];
void loop() {
  dcmotors.loop();
  servo_head.loop();

  current_time = millis();
  if (current_time - last_loop_time > 100) {
    dtostrf(hc.dist(), 10, 2, ultrasound_buff);
    client.publish("ultrasound", ultrasound_buff);
    last_loop_time = current_time;
  }

  if (!client.connected()) {
    reconnect();
  }
  client.loop();
}

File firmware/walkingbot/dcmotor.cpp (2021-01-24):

/*
Copyright (c) 2017, Agustin Devitturi (agustin.devitturi@gmail.com)
  This library is free software; you can redistribute it and/or
  modify it under the terms of the GNU Lesser General Public
  License as published by the Free Software Foundation; either
  version 2.1 of the License, or (at your option) any later version.
  This library is distributed in the hope that it will be useful,
  but WITHOUT ANY WARRANTY; without even the implied warranty of
  MERCHANTABILITY or FITNESS FOR A PARTICULAR PURPOSE.  See the GNU
  Lesser General Public License for more details.
  You should have received a copy of the GNU Lesser General Public
  License along with this library; if not, write to the Free Software
  Foundation, Inc., 51 Franklin St, Fifth Floor, Boston, MA  02110-1301  USA
*/

#include "dcmotor.h"

namespace L298N{

static const unsigned long LOOP_INTERVAL = 100;
static const int MAX_SPEED = 100;
static const int MIN_SPEED = 10;
static const int PWM_FREQ = 100;

DcMotors::DcMotors(int pin_en_a, int pin_en_b, int pin_dir1, int pin_dir2, int pin_dir3, int pin_dir4) {
	pin_en_a_ = pin_en_a;
	pin_en_b_ = pin_en_b;
	pin_dir1_ = pin_dir1;
	pin_dir2_ = pin_dir2;
	pin_dir3_ = pin_dir3;
	pin_dir4_ = pin_dir4;
	pinMode(pin_en_a_, OUTPUT);
  pinMode(pin_en_b_, OUTPUT);
  pinMode(pin_dir1_, OUTPUT);
  pinMode(pin_dir2_, OUTPUT);
  pinMode(pin_dir3_, OUTPUT);
  pinMode(pin_dir4_, OUTPUT);

  analogWriteRange(MAX_SPEED);
  analogWriteFreq(PWM_FREQ);
}

void DcMotors::loop() {
	unsigned long current_time = millis();
	if (current_time - last_loop_time_ > LOOP_INTERVAL) {
		do_loop();
		last_loop_time_ = current_time;
	}	
}

void DcMotors::do_loop() {
	update_speed();
}

void DcMotors::update_speed() {
	set_left_speed_instant(left_speed_ + compute_speed_ramp_ratio(left_speed_setpoint_, left_speed_));
	set_right_speed_instant(right_speed_ + compute_speed_ramp_ratio(right_speed_setpoint_, right_speed_));
}

int DcMotors::compute_speed_ramp_ratio(int speed_setpoint, int current_speed) {
	int speed_error = speed_setpoint - current_speed;
	if (speed_error == 0) {
		return speed_error;
	}

	int ramp_ratio;
	if (abs(speed_error) >= ramp_speed_) {
		ramp_ratio = ramp_speed_;
	} else {
		ramp_ratio = abs(speed_error);
	}
	if (speed_error > 0) {
		return ramp_ratio;
	} else  {
		return ramp_ratio * (-1); 
	}
}

int DcMotors::compute_speed_setpoint(int speed) {
	if (abs(speed) > MAX_SPEED) {
		if (speed >= 0) {
			speed = MAX_SPEED;
		} else {
			speed = -1 * MAX_SPEED;
		}
	}
	if (abs(speed) < MIN_SPEED) {
		speed = 0;
	}
	return speed;	
}

int DcMotors::get_right_speed() {
	return right_speed_;
}

int DcMotors::get_left_speed() {
	return left_speed_;
}


void DcMotors::set_right_speed_instant(int speed) {
	if (right_speed_ == speed) {
		return;
	}

  if (speed > 0) {
		digitalWrite(pin_dir2_, LOW);
  	digitalWrite(pin_dir1_, HIGH);
	} else if (speed < 0) {
		digitalWrite(pin_dir2_, HIGH);
  	digitalWrite(pin_dir1_, LOW);
	} else {
		digitalWrite(pin_dir2_, LOW);
  	digitalWrite(pin_dir1_, LOW);	
	}
  analogWrite(pin_en_a_, abs(speed));
  right_speed_ = speed;
}

void DcMotors::set_left_speed_instant(int speed) {
	if (left_speed_ == speed) {
		return;
	}

	if (speed > 0) {
		digitalWrite(pin_dir3_, LOW);
  	digitalWrite(pin_dir4_, HIGH);
	} else if (speed < 0) {
		digitalWrite(pin_dir3_, HIGH);
  	digitalWrite(pin_dir4_, LOW);
	} else {
		digitalWrite(pin_dir3_, LOW);
  	digitalWrite(pin_dir4_, LOW);	
	}
  analogWrite(pin_en_b_, abs(speed));
  left_speed_ = speed;
}

// DIFF DRIVE ECUATIONS
// VL = (Vr + Vl) / 2 	
// W = (Vr - Vl) / d

// Vr = VL + W * d/2
// Vl = VL - W * d/2

// VL : linear speed
// W : angular speed
// d : distance between wheels / legs
// Vr : right wheel speed (tangent to the ground) 
// Vl : left wheel speed (tangent to the ground)

void DcMotors::set_diff_drive_speed(int linear, int angular) {
	right_speed_setpoint_ = compute_speed_setpoint(linear + angular);
	left_speed_setpoint_ = compute_speed_setpoint(linear - angular);
}

} // namespace L298N

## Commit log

2021-01-24 Updated library and added node-red flow
2021-01-25 added parts trs and image directories.
    [DCMotor.ipt, Servo.ipt, base-bone.ipt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]
2021-01-26 Added circuit diagram
